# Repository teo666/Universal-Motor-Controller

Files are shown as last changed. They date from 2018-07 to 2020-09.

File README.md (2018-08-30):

# What Universal-Motor-Controller is

Universal-Motor-Controller (UMC) is an Arduino based software and hardware intended to drive universal brushed motor, like many circuit based on TDA1085.

# Main components

UMC consist of two parts:
- software: a C/C++ code running on Atmel Atmega-328p (Arduino Uno and compatibles boards)
- hardware: divided in three parts
    - zero crossing detector circuit (zcd), used for synchronize Arduino on main power
    - power circuit, used for feed motor
    - feedback circuit, used for monitoring the speed of the motor and adjust feed power consequently

# Working principle

Image below shows UMC's working diagram

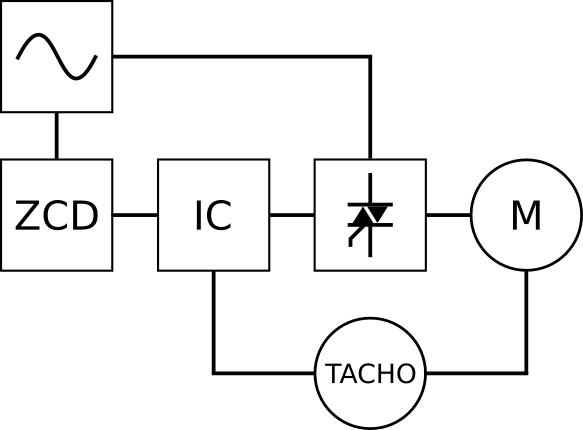
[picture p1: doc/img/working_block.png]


- The main power is connected to zero crossing detector circuit that transform sine wave signal to a square wave signal and send it to IC, main power source is conneted to motor power switching circuit
- IC is an Atmega-328p
- the power switching circuit is for made up of a triac, it controls the power of the motor and it is drived by IC
- the tacho is the feedback circuit of the system, it generate a signal to IC in relation to motor speed.

The main target of the driver is to changes power feeding the motor to prevent slowdowns when the load changes, to achieve this goal IC analyzes signal coming from tachogenerator and consequntly it swiches triac.

For a correct switching, IC has to know the exact phase of main power source, this is guarantee by ZCD circuit.

ZCD generates a square wave with a doubled frequency compared to main power source frequency, in my case, considering a 50Hz main frequency it generate a square wave of 100Hz.
This signal is connected to a special pin of the Atmega that is able to recognize the rising edge of ZCD output signal and rise a hardware interrupt that freeze the current program execution flow and execute a special routine. This mechanism allow to the Atmega to know when the main power source has reached the value of 0 volt so that it can syncronyze the motor power circuit.

(For a more comprensive and detailed guide about triac working principle read https://en.wikipedia.org/wiki/Thyristor and https://en.wikipedia.org/wiki/TRIAC)

The above simple mechanism is enough to drive motors and it allows to change their speed with a potentiometer, for example we could read an analog value and map it along the time interval punctuated by two rising edge coming from ZCD circuit, and switch triac in relation to that value. The figure below illustrate that mechanism

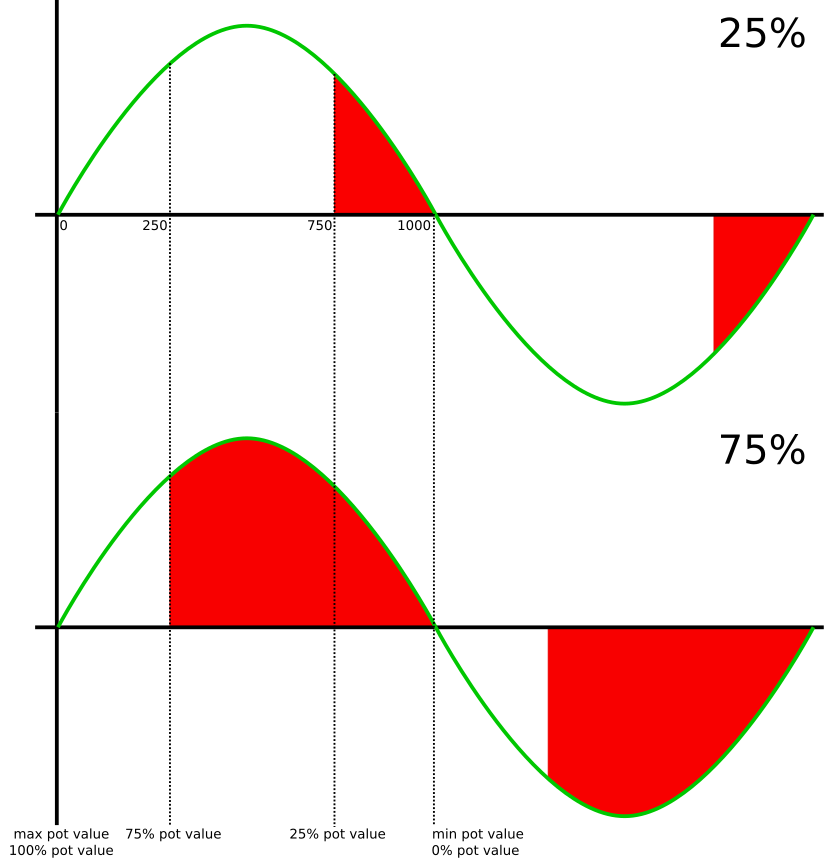
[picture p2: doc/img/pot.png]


Suppose to have a potentiometer to adjust the motor power: if potentiometer is turned to left the motor power decrease otherwise it increase. To achive that we have to change the switching point of triac inside main power source half period. In our case the potentiometer is connected to one of the avr analog input pin and readed value from potentiometer is mapped into a value between 0 and 999, and assume that we divide the semiperiord in 999 slice with the same width going from 0 to 999.

Now, if the potentiometer read value is 0 we want the mimimun motor power so we have to leave triac turned off.
If potentiometer get a value of 999 the desire power is maximum, we have to excite trigger immidiatly after the 0 volt point, or equivalentemente at 0th slice.
For any other value of potentiometer we have to trigger triac at slice numbered as (999 - pot_value) where pot_value is the value readed from potentiometer.

At this point the main question is: how divide half period into equal slices to know when turn on triac?
The response is: with timers.

Basically timers are hardware device enclosed into many ICs (avrs too) that can be used to count time. Think about timer like an unsigned variable going from 0 to a max value, and its content is increased by one (or decreased by one, or set to zero) every time that something happen, the something that happens is the clock signal, eventually scaled by a constant. Hardware can be configured to execute some special code (exactly like interrupt mechanism previously described) each time timer value reaches a special value, for example its maximum value.

The Atmega-328p (like arduino) is usually clocked with a 16MHz crystal oscillator, suppose to scale the clock with a 128 factor and use that signal to feed a 8bit timer. With that configuration timer increase its value by one every 
1 / (16e6 / 128) = 0.000008 seconds or 8 microseconds, and suppose to configure hardware to execute the special code (called Interrupt Service Routine or ISR) every time timer reach maximum value that in a 8bit configuration is 255, and the ISR increase the `tick_count` variable value by one starting from 0.

After 256 * 8 = 2048 microseconds `tick_count` value is incresed to 1  
After 4096 microsecond `tick_count` value is 2  
After 6144 microsecond `tick_count` value is 3  
After 8192 microsecond `tick_count` value is 4  
...  
After 999424 microseconds `tick_count` value is 488

or equivalently, when `tick_count` is 488 approximately a seconds is passed, that is how Arduino libraries implements millis, micros and delay functions.

The idea that we use is the same: increase a variable by one periodically inside the timer's overflow ISR (executed when timer reaches its maximum value) and reset it when ZCD find a zero volt point... then reapeat.

Go back to potentiometer example. Suppose to be immediatly after a 0 volt point and ZCD has reset our variable, and also use following condition to turn on triac.

``` c++
if( tick_count >= (999 - pot_value)){
    turn_on_triac();
}
```
- if potentiometer is set to maximum value (999) then (999 - pot_value) = 0, our variable is greater or equal to 0 and the triac is turned on
- if potentiometer is set to minimum value (0) then (999 - pot_value) = 999, our variable is less than 999 and the triac remains off
- likewise intermediate values

when next 0 volt poin occur, ZCD interrupt is executed, the `tick_count` variable is reset, and the process is repeated.

At this point we have a mixture of software and hardware that is commoly called *dimmer*, a device that can change power given to a load turning a potentiometer, those kind of devices are usually used to change halogen lamps brightness, the next step is feedback circuit integration.

The feedback circuit allow system to react to load changes and increase motor power to avoid slowdowns. The feedback circuit receives a signal coming from the tachogenerator of the motor, make some process on it and send it to IC.
The tachogenerator signal is commonly an AC sine wave signal that increase its frequency and voltage as the speed increases, so it is possible use frequency or voltage or event both together to analyze the speed of the motor, in UMC frequency is used.
The tacho AC signal is converted to an AC square wave signal and then only the positive component is taken, giving to IC a DC square wave signal. The figure below show the tacho processing signal

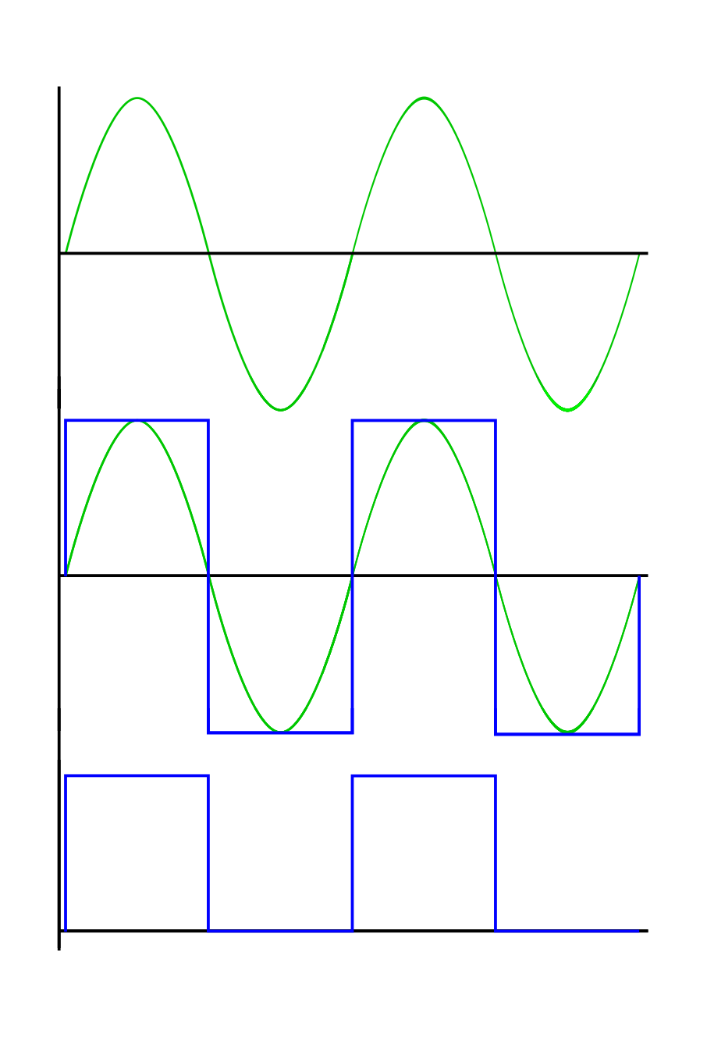
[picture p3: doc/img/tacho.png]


Once IC receives the feedback signal it has to get its frequency to know the actual speed motor and change its power consequently. To do that UMC use the same tecnique used for ZCD: interrupt mechanism.

Each time feedback signal goes from low to high (rising edge) IC's hardware generates an interrupt, the normal code execution is paused and associated ISR is executed.  
Previously we have talked about measuring signal frequency, in truth we do not need know the exact frequency, instead just a value related to frequency on wich make a comparison.  
At this point is relatively simple to get an evaluation of feedback signal frequency. Do you remember the use of timer for periodically check if triac has to be turned on? Ok, we use the same routine for increase a counter associated to feedback signal and we will reset that value in ISR associated to feedback rising edge event. In that manner we have a value related to frequency: the higher the frequency (motor speed) the lower is the couter.

At this point IC has all needed parameter for controlling power motor, and for do that we use a PID controller, you can read more about PID controller on [Wikipedia](https://en.wikipedia.org/wiki/PID_controller), about 
[used library](https://playground.arduino.cc/Code/PIDLibrary) and 
[detailed library explanation](http://brettbeauregard.com/blog/2011/04/improving-the-beginners-pid-introduction/).

# Hardware
DISCLAIMER: I am not a electrical engineer and all these circuits were taken on web and put together with a limited knowledge of them. If you have suggest to improve them and UMC you are welcome.

Below are reported the schematic circuits used in UMC
### Zero crossing detector circuit



note: VCC is 5 volt, all resistor are 1/4 watt,T1 and OK1 can be changed with equivalent components.  
PORTD,PIN2 is equivalent to pin 2 on Arduino-UNO board

### Motor power circuit



note: all resisor are 1/4 watt except R8 that is 1 watt (instead one 100 ohm resistor i recilced four 470 ohm resistor in parallel) , C3 must have appropriate galvanic isolation, for T2 I used a BTB16 couse BT138 gave me some problem.  

PORTD,PIN7 is equivalent to pin 7 on Arduino-UNO board

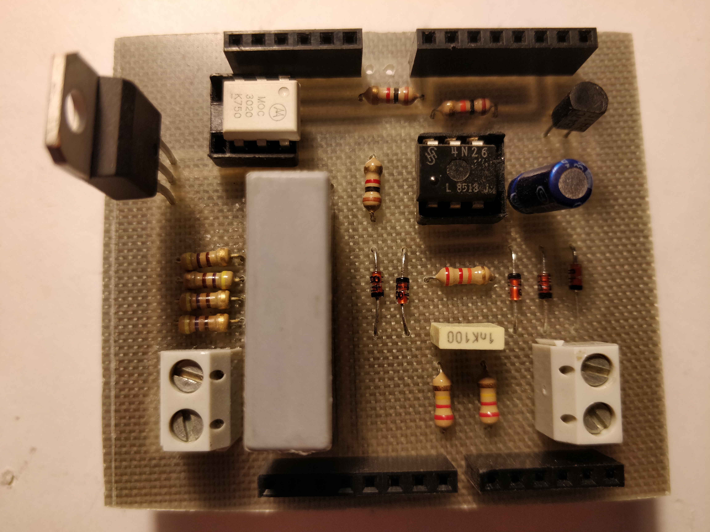
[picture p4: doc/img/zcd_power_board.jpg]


note: zcd and motor power circuits on same pcb



### Feedback circuit

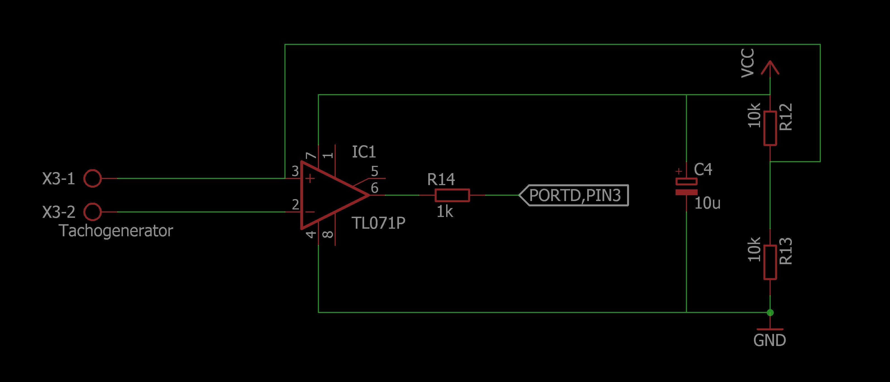
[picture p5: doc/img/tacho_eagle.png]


note: note: all resisor are 1/4 watt, Vcc is 9 volts, IC1 can be replaced with another opamp  

PORTD,PIN3 is equivalent to pin 3 on Arduino-UNO board

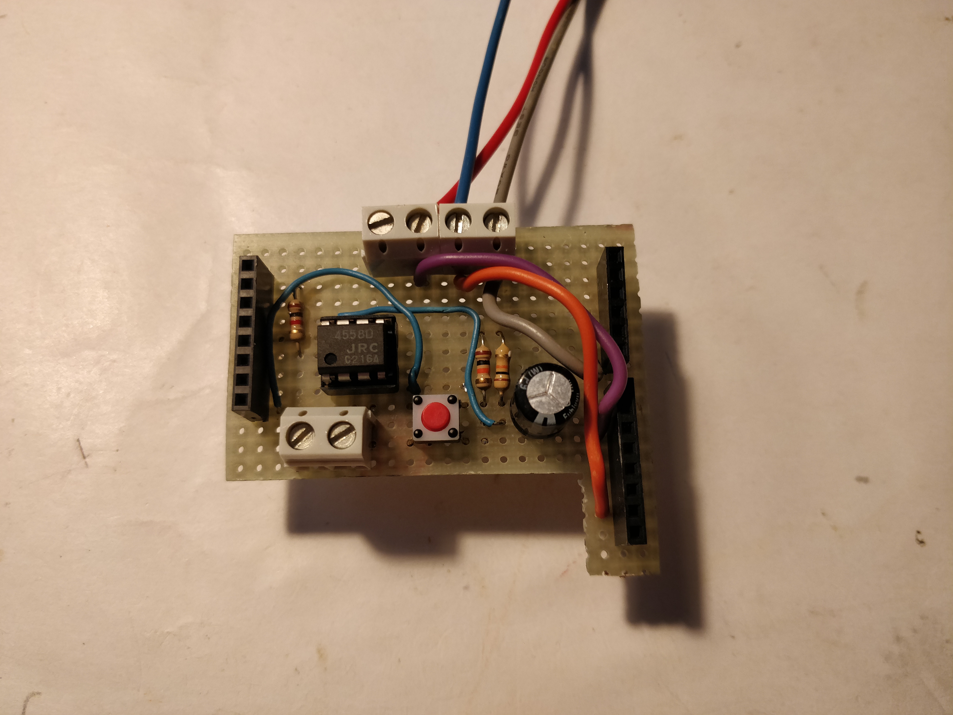
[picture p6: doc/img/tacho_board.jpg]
  

this board contains the potentiometer connector too and a push button connected to PORTD,PIN6 that is equivalent to pin 6 on Arduino-UNO board. We will talk about the push button later.

All together

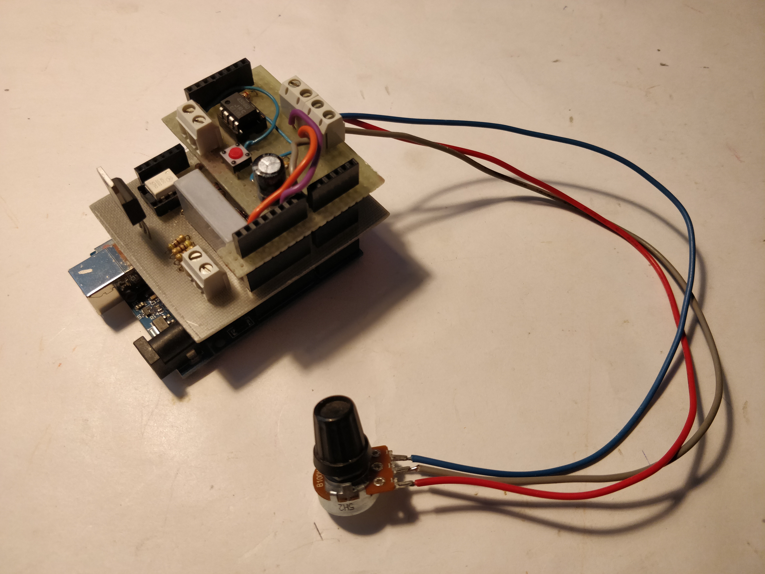
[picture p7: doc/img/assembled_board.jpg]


### Motor connection

Usually universal motor has six cable:
- two for the rotor
- two for the stator
- two for the tachogenerator

The cables of tachogenerator have to be connected to the tacho circuit and the order is irrilevant.  
The rotor and stator windings have to be connected in series togheter with main AC power source and power circuit, as show below.  
**NOTE: swap stator terminals to change rotation direction of the motor.**

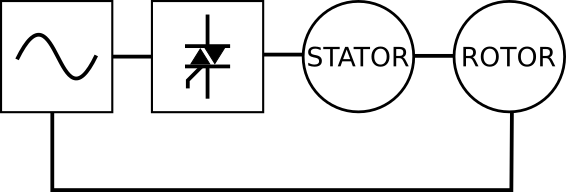
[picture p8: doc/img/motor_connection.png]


### UMC box

This photo show UMC with its box, taken from an old ATX power supply

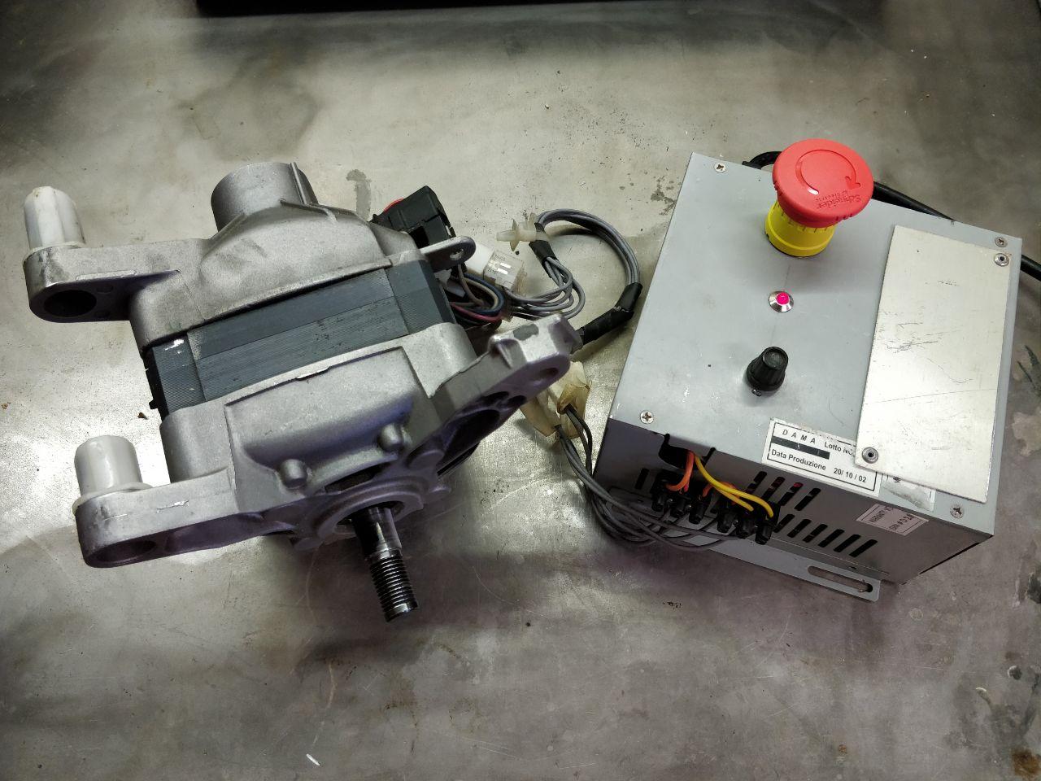
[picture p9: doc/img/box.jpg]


### Demo video

This [video](https://youtu.be/NKULTa6kquY) is a demonstration about UMC capabilities.  
This [video](https://youtu.be/l1mFbbu4X3Q) show capabilities of UMC on low speed.  
These two [video1](https://youtu.be/YVdLVX_Wkz4) and [video2](https://youtu.be/LLw0HUfIIPY) show a motor driven by UMC connected to a bench grindstone disconnected from main power.  
This [video](https://youtu.be/WyjBL2rSP_o) show UMC with current measurement.
# Speed limiter

UMC comes with a spftearec based speed limiter. Speed limiter use the feedback signal to to achive this goal. Speed limiter is usefull because it allow to map all potentiometer turning range inside the desired motor speed limits.  
In some application we could need maximum motor speed around 2000 rmp and in other 4000 rmp, but we want reach those speed when potentiometer is completely at the most, and leave hardware and software as they are, without needs of modifications.
At the moment it is possible limit the speed only during avr's boot process using the *programming button*.
Programming Button is a push button that if pressed connect PORTD,PIN6 (pin 6 of Arduino Uno) to ground, and allow us to set limit speed values (low and high), these values are stored in avr's EEPROM so they are accessible at the next restart, whitout needs to set up them every time.

**CAUTION: programming button is used to switch from automatic to manual mode too. Manual mode allow to disable the feedback circuit and use UMC as a simple dimmer. Suppose to have upper speed limit set to 1000 rpm and runnign motor with this speed, so with potentiometer at maximum. If you press programming button in this condition the motor will receice all possible power and its speed will increase with possible motor or equipment damage.**

### Usage

- Connect Arduino to PC, on Arduino IDE open serial monitor (ensure all parameter are correct: serial port, board etc)
- press and hold the *programming button*
- reset the board keeping *programming button* pressed
- read serial monitor keeping *programming button* pressed and follow printed instructions

At the end of process if you turn potentiometer the speed motor is limeted inside selected range.

# Configuration

Attention: before reading this section be sure that you know what PID parameters are, otherwise follow links at the end of "Working principle" section.

With 1.0.1 version UMC comes with dynamic PID parameter change. Basically UMC can change its PID parameter in relation to motor speed, in fact some parameters that work correctly at a fixed speed can be wrong at lower or higher speed, making UMC non-reactive or causing rotation spikes.  
To achive this gol the constructor of PID library take extra parameters, such as a function, that it is called inside `compute()` PID function to get the correct PID parameters.
That function is named `search` and it is placed inside `configuration.h` file. You have to customize `search` function to satisfy your preferences.
The signature of `search` function is the following
``` c++
CoefficientPtr search() {
    ...
}
```
it must return a `CoefficientPtr` that is define in `PID_ASYNC.h` as
``` c++
typedef struct _coefficient {
  double Kp;
  double Ki;
  double Kd;
} Coefficient;

typedef Coefficient *CoefficientPtr;
```
Inside `configuration.h` file you can find an example of search function that meets my needs, the code is the following
``` c++
//static parameter declaration
Coefficient k_param[9];

/**
* function called inside setup() to fetch parameter
*/
void init_params() {
  k_param[0].Kp = 0.3;
  k_param[0].Ki = 0.0001;
  k_param[0].Kd = 0;

  k_param[1].Kp = 0.8;
  k_param[1].Ki = 0.0001;
  k_param[1].Kd = 0;

  k_param[2].Kp = 1;
  k_param[2].Ki = 0.0001;
  k_param[2].Kd = 0;

  k_param[3].Kp = 1.5;
  k_param[3].Ki = 0.0002;
  k_param[3].Kd = 0;

  k_param[4].Kp = 2;
  k_param[4].Ki = 0.0002;
  k_param[4].Kd = 0;

  k_param[5].Kp = 3;
  k_param[5].Ki = 0.0002;
  k_param[5].Kd = 0;

  k_param[6].Kp = 3;
  k_param[6].Ki = 0.001;
  k_param[6].Kd = 0;

  k_param[7].Kp = 3;
  k_param[7].Ki = 0.001;
  k_param[7].Kd = 0;

  k_param[8].Kp = 7;
  k_param[8].Ki = 0.002;
  k_param[8].Kd = 0;
}

/**
 * function called inside compute() PID function
 * get the minimum value from Setpoint and Input 
 * and use it to chose the correct parameters
 */
CoefficientPtr search() {
  double _val = min(Setpoint, Input);
  uint8_t index = 0;

  if (_val >= 550) {
    index = 0;
  } else if (_val >= 500 && _val < 550) {
    index = 1;
  } else if (_val >= 450 && _val < 500) {
    index = 2;
  } else if (_val >= 400 && _val < 450) {
    index = 3;
  } else if (_val >= 350 && _val < 400) {
    index = 4;
  } else if (_val >= 250 && _val < 350) {
    index = 5;
  } else if (_val >= 200 && _val < 250) {
    index = 6;
  } else if (_val >= 150 && _val < 200) {
    index = 7;
  } else if (_val <= 150) {
    index = 8;
  }
  return &k_param[index];
}
```

- on the top an array is declared to hold different `Coefficient` structures,
- the method `init_params()` is declared, it allow you to initialize the array, in the above code it is initialized statically, but you could need to read some value from EEPROM and store them inside it.
- the `search` function is declared, it is responsible for providing dynamic parameters to PID in relation to the speed of the motor.

Inside `configuration.h` file you have access to all available global variables, for example Setpoint, Input and Output PID variables, but **DON'T MODIFY THEM, JUST READ THEM**.

Ok... but, where those value (500, 350 and so on) come from?  
They come from **test mode**. *test mode* allow you to run UMC, change speed with potentiometer and set dynamically PID parameters to test them with no need to flash the ROM of the avr everytime.
To use *test mode* uncomment first line in the `Universal_Motor_Controller.ino` file to get
``` c++
#define TEST_MODE
```
and then flash avr.  
Open serial monitor, current *Setpoint*, *Input* and *Output* values are shown. You can change the *kp*, *ki* and *kd* parameters in serial input, giving the command
``` bash
<param_name> <value>
```
where `param_name` can be 
``` bash
kp
ki
kd
```
to set respectively proportional, integral or derivative parameter  
and `value` is a floating point value like 
``` bash
0.0002
```
**ATTENTION: THERE IS ONLY ONE SPACE BERTWEEN TWO ARGUMENTS** 

**ATTENTION: PARAMETERS MUST BE GIVEN SEPARATELY, YOU CAN'T SET THEM ALL TOGHETER, ONLY ONE BY ONE**  

**ATTENTION: K-VALUES ARE SHOWN WITH EIGHT DECIMAL DIGIT PRECISION**

While program runs it shows current *Setpoint* and *Input* values that can be used to discriminate the correct PID weights inside *search* function, that is where previous unknow numbers come from. With these value it is possible to see how UMC react to load change, considering that *Input* value should be near as possible to *Setpoint*.

Once done you can create your own `init_params` and `search` function and comment first line into `Universal_Motor_Controller.ino` file to get
``` c++
//#define TEST_MODE
```
and flash again.

Enjoy!

# Changelog

v1.0.1
- UMC comes with its own version of PID library, it is heavily based on Brett Beauregard's PID library  
(library link:  https://playground.arduino.cc/Code/PIDLibrary  
email: <br3ttb@gmail.com>  
library explanation: http://brettbeauregard.com/blog/2011/04/improving-the-beginners-pid-introduction/): the new version is basically identical to Brett Beauregard's version except for the facts that it is now asynchronous and some unused methods are deleted.
- UMC can now change its PID parameters dynamically, related to motor speed.
- Improved motor stability on low speed
- Code revisiting.
- UMC comes now with a test mode usefull for calibration.

v1.0.2
- Improved initial frequency calculation by decreasing needed time
- Added zero crossing detection circuit fail detection condition. Before this version when a zcd circuit fail occur UMC gave all power to the motor
- Added motor hang/stop detection condition (early version to use with caution)
- UMC is now (partially) invulnerable to the power line frequency changes
- Added eagle project files including circuit schematic and board layout

# Known problems and Improvements

This is an early UMC version and there are many things to improve.  
I hope that someone will find this project interesting helping me (and diyers community) to improve its capabilities.

### Higher priority 
- Slow start integration (via PID controller)
- Allow rotation inversion (require hardware modification and hang/stop detection)

### Lower priority

- Lower speed limit can't be set to 0rpm.
- Program lives as it is, there isn't an Object Oriented Programming model and integrations with other libraries are difficult due to time dependent application nature.
- UMC doesn't allow connect multiple motor due low number of Atmega-328p interrupt pins. One is necessary for ZCD circuit the other for feedback circuit. I'm trying to remove this lack using a frequncy to analog converter that technically will allow drive up to six motor. Should be possible monitor feedback signal without the need of interrupt pin by checking it periodically inside timer's ISR, but I have not tested this method yet.
- OOP usage is releted to the above two problems.

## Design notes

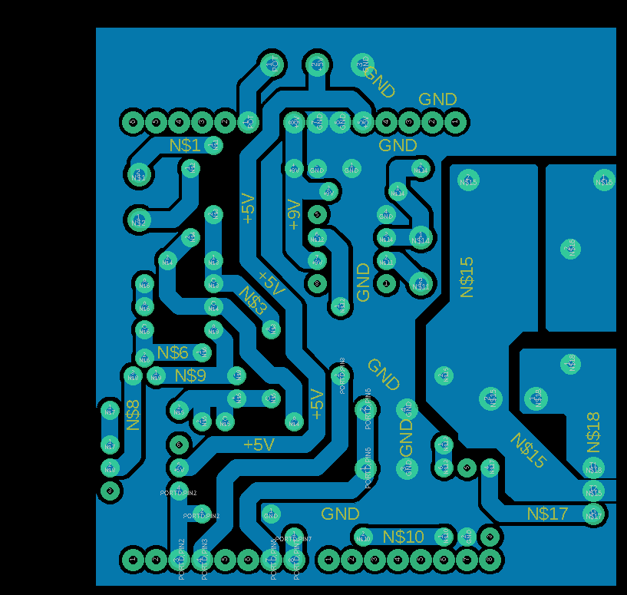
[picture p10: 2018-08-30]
doc/img/circuit-net.png

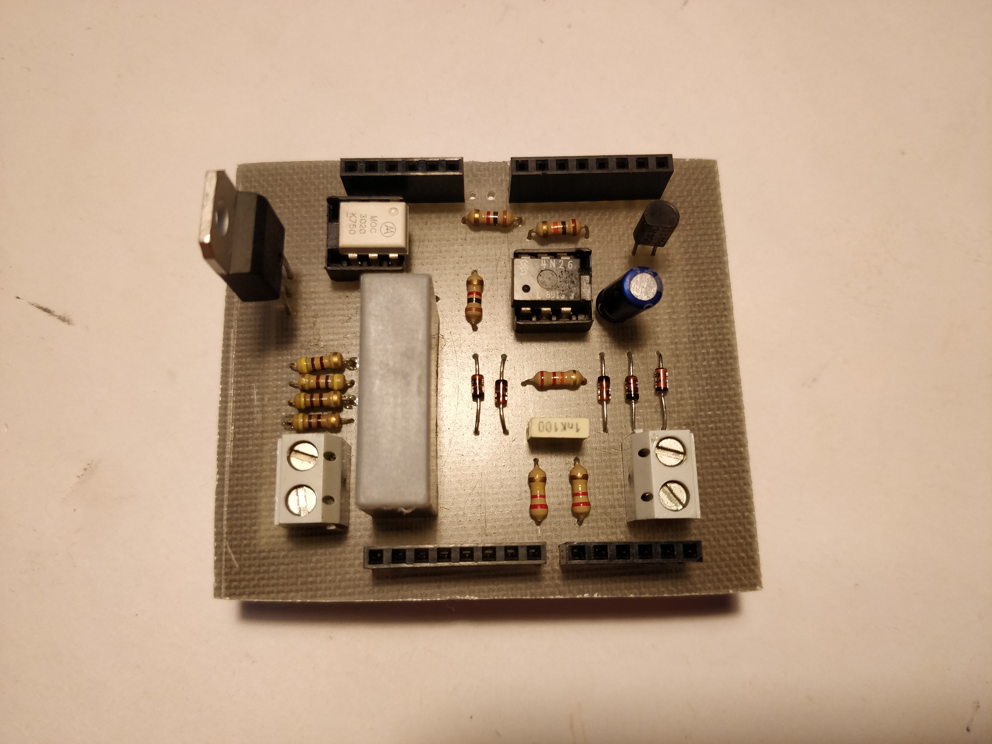
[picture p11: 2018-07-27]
doc/img/zcd_small_board.jpg

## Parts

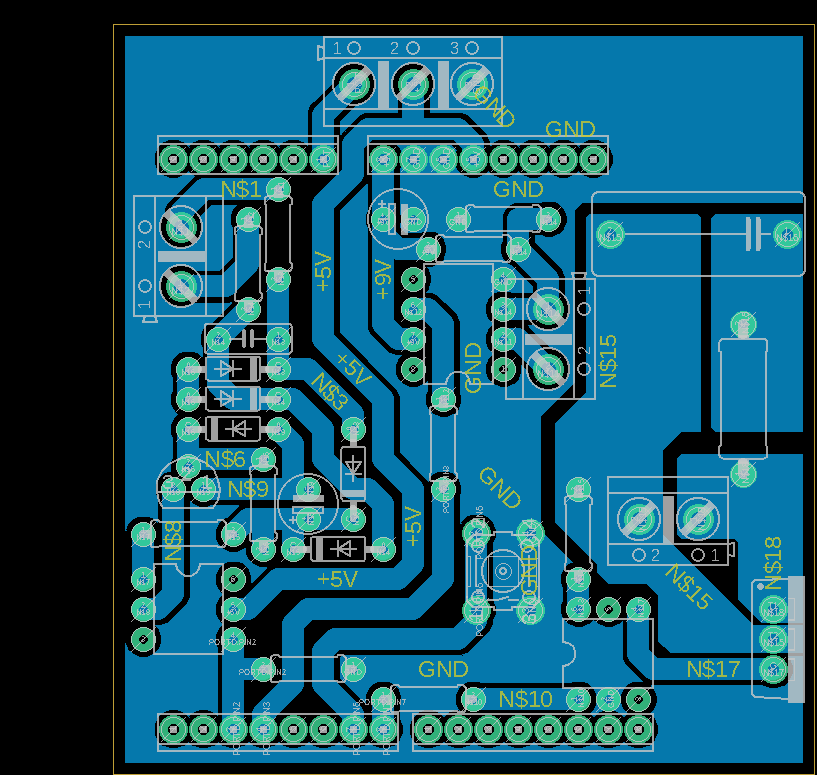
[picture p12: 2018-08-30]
doc/img/circuit-net-component.png

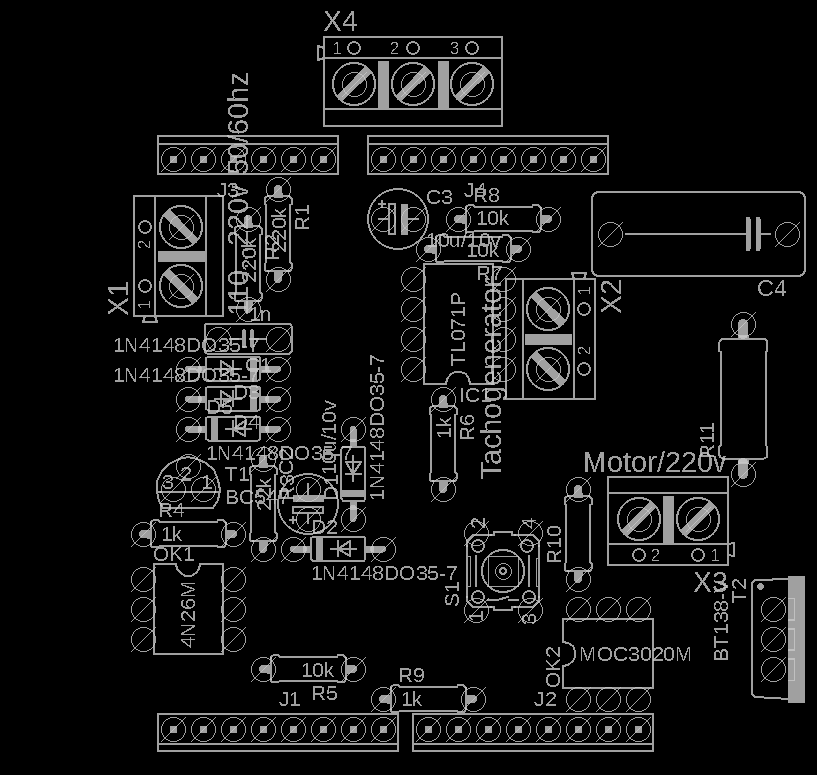
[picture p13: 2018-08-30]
doc/img/circuit-component.png

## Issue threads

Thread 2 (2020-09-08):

Compiling trouble

Baravantan, 2020-09-08:
First of all thank you for sharing your work.
I tried to compile with the "TEST_MODE" option but I get an error and it doesn't compile.
Also, if I leave the option commented out, I can compile in, but when I feed the circuit, the motor slowly begins to accelerate whatever the position of the potentiometer.
I checked the input signals (ZCD, TACHO, POT) and they seems normal.

versione 1.0.2 | Arduino:1.8.12 (Linux), Scheda:"Arduino Nano, ATmega328P (Old Bootloader)"

teo666, 2020-09-09:
Hi @Baravantan !
Thanks to you for use and improve this code. I hope it can be usefull for you.

1) I confirm the compile error, the problem was caused due to a wrong place regards macroes definition. I have updated the repo.
2) Have you set the speed limit values during start up? These value should be printed in console during board sturtup. Check them, if they are correct, try to enable test mode, change PID parameters and check if the motor react to these changes.

Let me know

Baravantan, 2020-09-09:
Hi @teo666 and thanks for your reply.
I was unable to set the speed limits values because, on power ON, the motor begins to accelerate whatever the position of the potentiometer, until it reaches a dangerous rpm. then I cannot set the minimum and maximum desired values. Unfortunately, my knowledge of the software is somewhat limited.
I built a circuit following the diagram you published, and connected it to a motor recovered from a Bosch washing machine, not better identified. I measured the signals on the tachometer more carefully and I detected **168Vpp** (!!)
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
and, on PORTD pin3, a signal at 25+ kHz and **8 Vpp** which I think is too much for Arduino.
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
Then, I lowered the supply voltage of the OP amp from 9V to 5.5V, obtaining the same signal at the output but with the correct level.
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
May be that my motor produces a too high TACHO signal, and saturate (or destroy!) the OP amp input?
I will do other tests. If you have any suggestion, please help me. Thanks

teo666, 2020-09-12:
Hi @Baravantan
I admin that my circuit is not perfect due I am a software engineer but  not electrical, it could be improved and if you have suggestion you are welcome.

The tacho circuit is intended to work in saturation, I use this method to convert the tacho signal into digital signal that is more
easy to analize in arduino thanks to interrups.

However you are describing an unexpected behavior in UMC. In fact when programming phase start the output pin should be disabled preventing motor to start spin.
In this phase the main line frequency is calculated and the output motor is directly drived by potentiometer value. So keeping potentiometer
at lowest value (or ground its input) should disable the output motor pin, and increasing the potentiometer value shoud give the ability to modulate motor speed whit no PID control.

So I think there should be upstream problem, and preceed by step, ensuring all circuits (and software) are working properly. First of all i suggest to make programming mode working proprerty. It is usefull cause its behavior is like a simple triac circuit and can be used to drive bulb lamp (no led or flourescent lamp) avoiding keep attention on motor speed.

I remember that to get in programming mode programming button must be pressed before arduino start booting, and keep it pressend until "Programming mode" appear in serial monitor.

At this point the main line frequency is calculated the result is printed on monitor (its  value is not printed ad frequency but as timer clock tick) and UMC ask to set limit speed values, with oscilloscope should be possible see on ZCD circuit output a signal as in following image. At this point tacho signal is useless (except if we continue with setting limit speed) and circuit could be used as a simple triac circuit.
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

Are you able to confirm these step?

PS: ZCD signal can be always measured to check it works properly, even in disconnected

The next step is check if arduino can trigger interrupt propertly
Obviously i take for granted that circuit is correct

Baravantan, 2020-09-13:
Hi, @teo666
Ok, I followed the suggested procedure:
By keeping S1 pressed at boot, it enters the programming mode correctly:
`Calculating frequency ...`
`Number of ticks per half period: 617`
`Programming mode`
`Release programming button, please`
BUT the engine always runs.
IF instead I press S1 when the sketch is running, with the POT at zero, the output goes to zero.

I tried, as suggested, to connect a light bulb instead of the motor (great suggestion!).
I took a couple of screenshots: ch1 ZCD (1 yellow) Pin2 || ch2 Pin OC (2 light blue) || ch3 ACL (3 fuchsia) || S1 OFF || POT 50%
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

the signal on OC (2) turns off after 640uS from the crossing of the zero of AC L (3), when the next half-wave has reached 50V, thus triggering the triac also for the next half-cycle and therefore leaving the output always on.
By holding S1 and turning the POT, the length of the signal on the OC changes to the left, but it always goes out in the same point, except when I turn the POT to zero: in this case the signal on the OC disappears completely, and then the output turns off .
What I would do, if I were able, is to anticipate the shutdown of OC (2) before the zero crossing.
What I don't understand is why the sketch on your circuit works, but on mine it doesn't.
I also double-checked the connections and tried to upload the sketch to Arduino UNO as well (I'm currently using Nano), with identical behavior.
I hope this information is somehow useful.
Thanks for your help.

Baravantan, 2020-09-14:
Hi, @teo666
Important update
I built a really rough circuit, with the aim of getting a signal when AC is below a certain voltage level, and then around the zero crossing.
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
The pulse I get is not that great (1 yellow), but now the circuit works in dimmer mode!
The ZCD pulse now arrives before the zero crossing, and consequently also the OC pin signal (2 light blue) turns off before it, but obviously not the triac, which continues to conduct up to the ZC.
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
Obviously, the circuit now needs some fine tuning and some calculations; what do you think about it?

Baravantan, 2020-09-15:
My idea (leaving the circuit as is) is to transform the output to the triac from variable to fixed width (some tens of µS) leaving unchanged the moment when it turns on. I tried to change it in the code, eg.
`if (tick_after_zcd > xx) {TURN_OFF_TRIAC (); triac_state = 0;}`
but I did not succeed.

teo666, 2020-09-15:
Hi @Baravantan
These images are extremely usefull because they describe the working princile, and help to find the error.

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

Good!

Lets analize [this](https://user-images.githubusercontent.com/11626439/93020077-e1a09400-f5e3-11ea-9e5a-24b2b3289924.png) image, and exlude momentary the fuchsia channel.
The yellow signal represent ZCD output and light blue triac triggering signal.

The fact that light blue signal overlaps the yellow one is a desired behavior, and this confirm that the interrupt code
is working correctly. This overlap is caused by the fact that the software make sure that zero crossing point is reached correctly and it is effectively the correct one.
This mechanism is used to avoid that arduino recognize signal spikes in ZCD signal as wrong zero point.

The following block code is responsible of this behavior, increasing the value (10) in the condition will delay triac output switch off.
If 0 is used no correction will be used and falling edge of triac output will coincide with rising edge of ZDC signal, and using too much higher value will
fall triac output switch off after the zero crossing point, thus making triac always on.

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

The ZCD circuit that you have used confirm this situation, except the fact that it doesn't give a sqaure wave signal, we can see the same overlapping situation
in [this](https://user-images.githubusercontent.com/11626439/93047871-2705a580-f666-11ea-9664-b1d292cad140.png image.

At this point cosider the [image](https://user-images.githubusercontent.com/11626439/93020077-e1a09400-f5e3-11ea-9e5a-24b2b3289924.png) with fuchsia channel.

My ZCD circuit is based on [this](https://dextrel.net/design-ideas-2/mains-zero-crossing-detector.html) and as the author explain it should
trigger around zero volt point. BUT previous image seems not to confirm this situation, in fact the yellow risign edge is shifted to the right.

So I can assert that ZCD is not working propertly. Your circuit insead is working correctly becuase the yellow spike is centered on zero point.

At this point we have many way to proceed, some are solutions, others dummies solutions:

Solution:
    Change ZCD circuit.

Dummy solutions:
    Turn off triac output signal earlier for example after triac has entered into conduction state (I don't consider this as solution becuase does not resolve the sync problem of ZCD signal)

teo666, 2020-09-15:
> My idea (leaving the circuit as is) is to transform the output to the triac from variable to fixed width (some tens of µS) leaving unchanged the moment when it turns on. I tried to change it in the code, eg.
> `if (tick_after_zcd > xx) {TURN_OFF_TRIAC (); triac_state = 0;}`
> but I did not succeed.

I can suggest this fast, brutal and not tested code

`if (triac_state) {`
`TURN_OFF_TRIAC();`
` }`

and put it immediatly BEFORE this code (before triac hes been swiched on)

`if (tick_after_zcd >= output && !triac_state) {`
`    // accendi il triac`
`    TURN_ON_TRIAC();`
`    triac_state = 1;`
`  }`

Let me know
Teo

Baravantan, 2020-09-16:
It finally works as expected! and leaving yours circuit and sw intact.
Solution:
Put the correct values of the components on the circuit.

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

As I feared, this was human error: for reasons too long to explain, I put C2 100x the required value. I'm sorry.
"C2 forms together with R1 and R2 a first-order low pass filter (...) By decreasing the 1/f frequency of this filter (...) the ZC-pulse will be delayed in relation to the real mains zero crossings"

Thank you very much for the time you have dedicated to me to find the error, as well as your indications were very useful to understand how your circuit works.

Giovanni

Closed 2020-09-16.

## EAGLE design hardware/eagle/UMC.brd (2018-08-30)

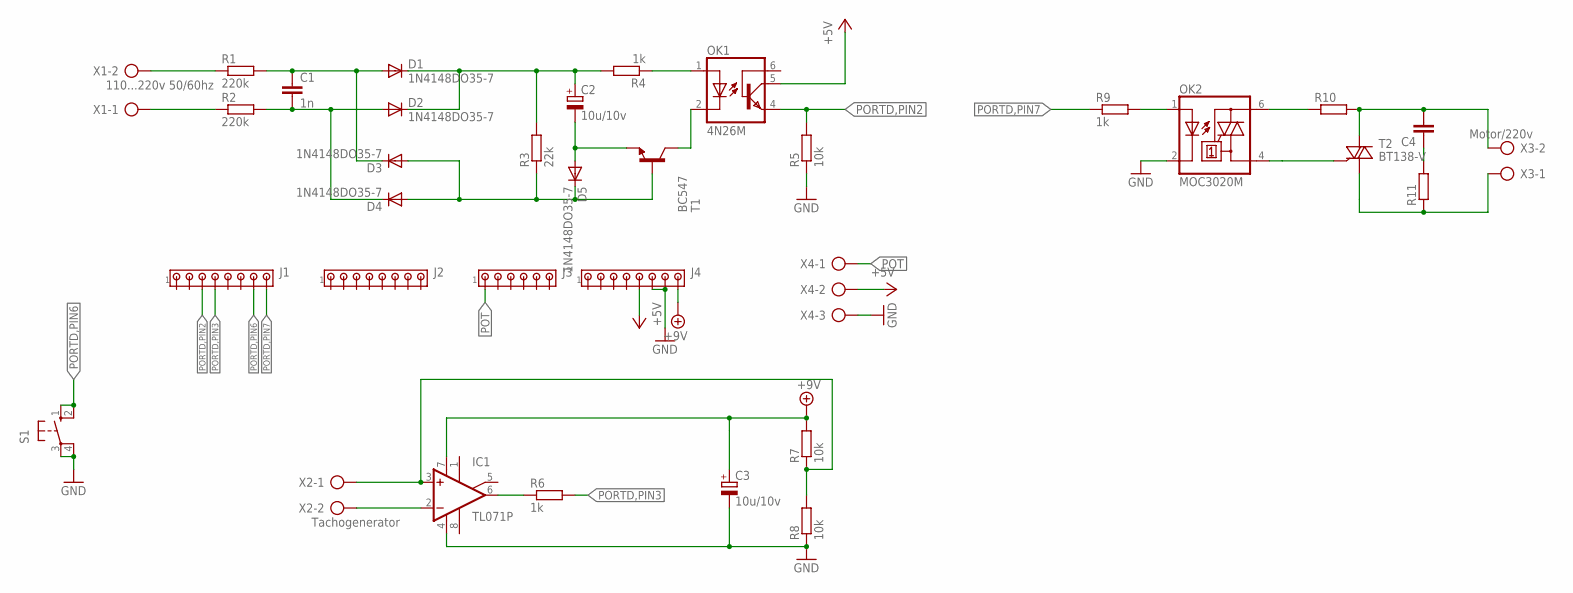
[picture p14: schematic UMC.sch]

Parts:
C1: 1n; C5B2.5
C2, C3: 10u/10v; E2,5-5
C4: C15/7; C15B7
D1, D2, D3, D4, D5: 1N4148DO35-7; DO35-7
IC1: TL071P; DIL08
J1, J2, J4: MTA08-100; 10X08MTA
J3: MTA06-100; 10X06MTA
OK1: 4N26M; DIL06
OK2: MOC3020M; DIL06
R1, R2: 220k; 0207/7
R3: 22k; 0207/7
R4, R6, R9: 1k; 0207/7
R5, R7, R8: 10k; 0207/7
R10: R-EU_0207/7; 0207/7
R11: R-EU_0411/12; 0411/12
S1: 10-XX; B3F-10XX
T1: BC547; TO92
T2: BT138-V; TO220BV
X1: 110...220v 50/60hz; AK500/2
X2: Tachogenerator; AK500/2
X3: Motor/220v; AK500/2
X4: AK500/3

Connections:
+5V: J4.5, OK1.5 (COL), X4.2
+9V: C3.+, IC1.7 (V+), J4.8, R7.2
GND: C3.-, IC1.4 (V-), J4.6, J4.7, OK2.2 (C), R5.1, R8.1, S1.3, S1.4 (P1), X4.3
unnamed: R1.1, X1.2
unnamed: R2.1, X1.1
unnamed: C1.1, D1.A, D3.C, R1.2
unnamed: C1.2, D2.A, D4.C, R2.2
unnamed: C2.+, D1.C, D2.C, R3.2, R4.2
unnamed: D3.A, D4.A, D5.C, R3.1, T1.2 (B)
unnamed: OK1.1 (A), R4.1
unnamed: OK1.2 (C), T1.3 (C)
unnamed: C2.-, D5.A, T1.1 (E)
unnamed: OK2.1 (A), R9.2
unnamed: IC1.2 (-IN), X2.2
unnamed: IC1.6 (OUT), R6.1
unnamed: OK2.6 (A2), R10.1
unnamed: IC1.3 (+IN), R7.1, R8.2, X2.1
unnamed: C4.2, R10.2, T2.T2 (A2), X3.2
unnamed: C4.1, R11.2
unnamed: OK2.4 (A1), T2.G
unnamed: R11.1, T2.T1 (A1), X3.1
PORTD,PIN2: J1.3, OK1.4 (EMI), R5.2
PORTD,PIN3: J1.4, R6.2
PORTD,PIN6: J1.7, S1.1 (S), S1.2 (S1)
PORTD,PIN7: J1.8, R9.1
POT: J3.1, X4.1

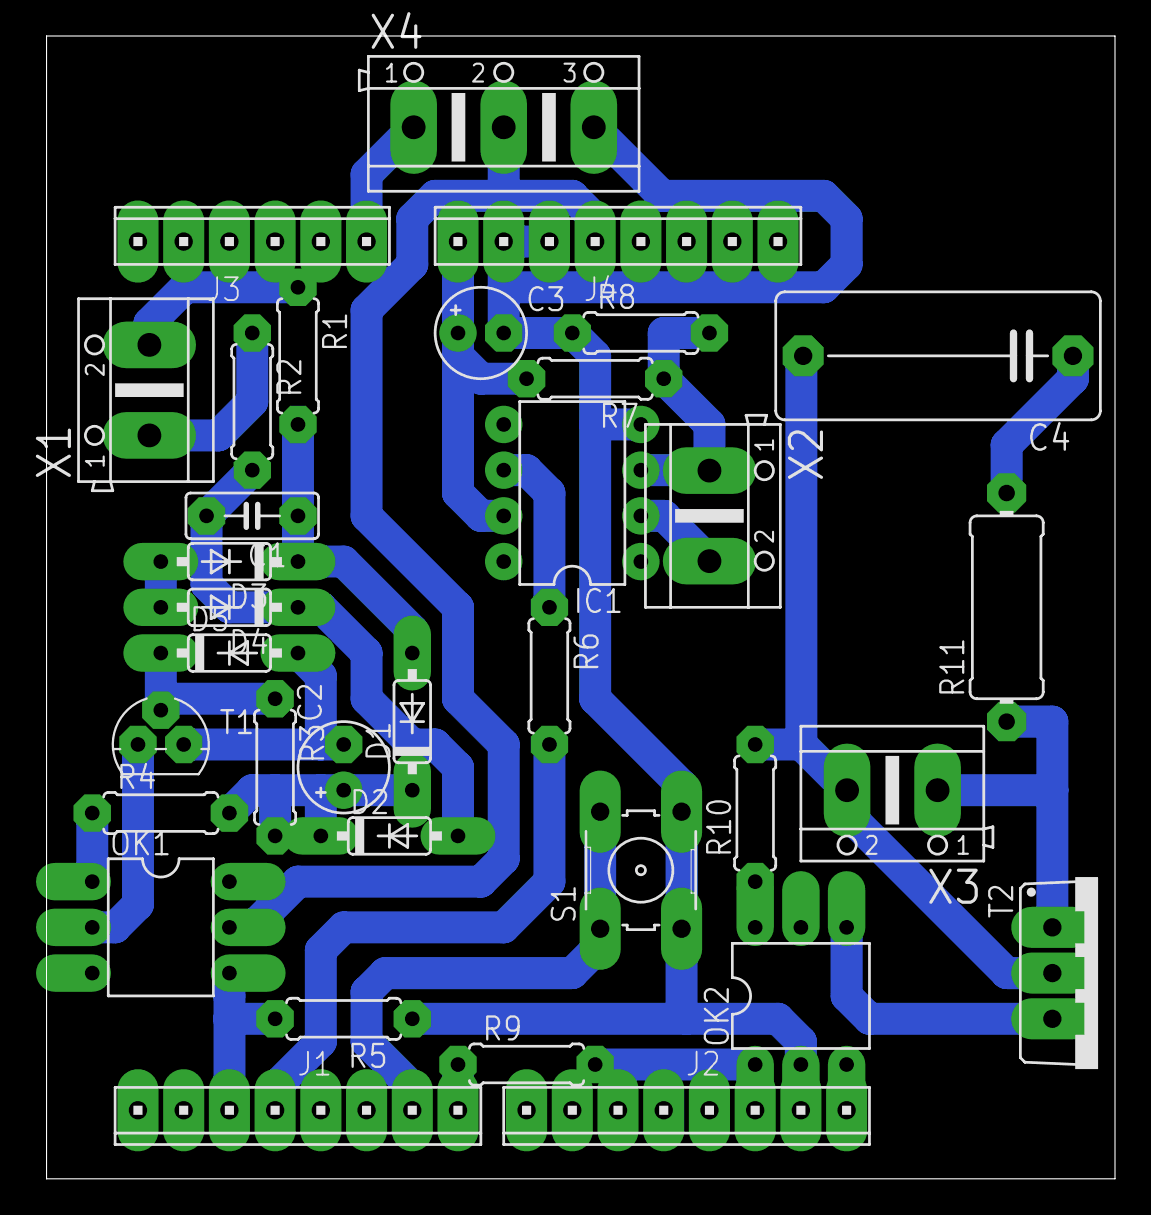
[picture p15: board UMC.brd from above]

Board: 2 copper layers, 59.4 x 63.5 mm, 34 parts (0 on the bottom side), 26 nets.

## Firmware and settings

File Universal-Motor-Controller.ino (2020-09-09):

/**********************************************************************************************
 * Arduino Universal Motor Controller - Version 1.0.2
 * by teo Basili <basili.teo@gmail.com> https://github.com/teo666
 **********************************************************************************************/

//#define TEST_MODE

#include "PID_ASYNC.h"
#include "pin_definition.h"

#define ZCD_FAIL_LIMIT 2500
#define TACHO_FAIL_LIMIT 5000

#include <EEPROM.h>

PID *motor_PID;

volatile uint16_t zcd_tick_log = 0;
volatile uint16_t tacho_tick_log = 0;
volatile uint16_t tick_after_zcd = 0;
volatile uint16_t tick_after_tacho = 0;
volatile uint8_t triac_state = 0;

// questa cosa del delay count mi serve per evitare di usare le funzioni di
// tempo di arduino
volatile uint8_t delay_count = 0;
volatile uint8_t delay_allow = 0;

uint16_t tick_per_phase = 0;

/*in alcune circostanze (dovute a problemi induttivi dal momento che ho potuto
registrarli solamente a motore connesso???) capita che il circuito zcd presenti
dei disturbi che fanno si' che alla sua uscita compaiano dei picchi di tensione
che alterano il corretto fasamento; questi picchi tuttavia hanno una durata
molto breve rispetto al tempo in cui l'onda quadra dello zcd si trova a livello
logico alto, per cui utilizzo questa variabile per distinguere tali valori

- al cambiamento dello stato di uscita dello zdc azzero dei parametri, compreso
zcd_error_correction
- controllo periodicamente (nell-interrupt del timer) il valore di ingresso
dello zcd: se e' HIGH incremento zcd_error_correction altrimenti non faccio
niente
- se dopo un po' di tempo tale valore raggiunge un valore limite (10) allora la
mi sto trovando nel punto un cui lo zcd e' effettivamente in fase e non si e'
presentato il disturbo
*/
volatile uint8_t zcd_error_correction = 0;
volatile uint8_t found_correct_main_phase = 0;

volatile uint8_t tacho_error_correction = 0;
volatile uint8_t found_correct_tacho_phase = 0;

/*
variabili per la lettura dei valori analogici, contengono il valore delle
letture
*/
volatile uint8_t HIGH_ANALOG_REG = 0;
volatile uint8_t LOW_ANALOG_REG = 0;

volatile uint8_t frequency_calc_added = 0;

// il range dell' output va da 0 a 485, a 0 il motore gira a foo 485 val minimo
volatile uint16_t output = 65535; // max value
volatile uint16_t tacho_min_speed_value = 0;
volatile uint16_t tacho_max_speed_value = 0;

uint16_t output_min_speed_value = 0;
uint16_t output_max_speed_value = 0;

// variabili del pid

double Setpoint, Input, Output;
volatile uint8_t computeBarrier = 0;

volatile uint16_t delay_counter = 0;
volatile uint16_t last_delay_counter = 0;

//////////////////// FUNZIONI DI UTILITA' ///////////////////////

uint8_t my_digital_read(uint8_t port_reg, uint8_t bit) {
  if (port_reg & _BV(bit))
    return 1;
  return 0;
}

void limit(volatile uint16_t *val, uint16_t min, uint16_t max) {
  if (*val > max) {
    *val = max;
  } else if (*val < min) {
    *val = min;
  }
}

uint16_t calculate_main_power_frequency() {
  uint8_t frequency_calc = 0;
  uint32_t tick_sum = 0;

  while (frequency_calc < 20) {
    if (frequency_calc_added) {
      frequency_calc_added = 0;
      tick_sum += zcd_tick_log;
      frequency_calc++;
    }
  }

  return tick_sum / 20;
}

void check_programming_button() {
  // se il bottone e' pigiato chiededre di rilasciarlo
  if (!my_digital_read(PIND, PROG_PIN)) {
    Serial.println("Release programming button, please");
    while (!my_digital_read(PIND, PROG_PIN)) {
    }
  }
}

void button_hold_request(void (*loop)(), void (*on_exit)()) {
  while (1) {
    loop();
    if (delay_allow) {
      on_exit();
      break;
    }
  }
}

void loop_read_fun() {
  output =
      map((HIGH_ANALOG_REG << 8) | LOW_ANALOG_REG, 1023, 0, 0, tick_per_phase);
}

//////////////////////////////////////////////////////////////////////

void save_low_speed_exit_fun() {
  tacho_min_speed_value = tacho_tick_log;
  output_min_speed_value = output;
  EEPROM.write(0, tacho_min_speed_value >> 8);
  EEPROM.write(1, tacho_min_speed_value);
  EEPROM.write(2, output_min_speed_value >> 8);
  EEPROM.write(3, output_min_speed_value);
  Serial.print(F("LOW speed tacho set to: "));
  Serial.print(tacho_min_speed_value);
  Serial.print(F(" LOW speed output set to: "));
  Serial.print(output_min_speed_value);
  Serial.println(F(", saving ..."));
}

void save_high_speed_exit_fun() {
  tacho_max_speed_value = tacho_tick_log;
  output_max_speed_value = output;
  if (tacho_max_speed_value > tacho_min_speed_value) {
    Serial.println(F("The HIGH speed must be higher than LOW speed"));
    // se il bottone e' pigiato chiededre di rilasciarlo
    check_programming_button();
    Serial.println(F("try again"));
  } else {
    EEPROM.write(4, tacho_max_speed_value >> 8);
    EEPROM.write(5, tacho_max_speed_value);
    EEPROM.write(6, output_max_speed_value >> 8);
    EEPROM.write(7, output_max_speed_value);
    Serial.print(F("HIGH speed tacho set to: "));
    Serial.print(tacho_max_speed_value);
    Serial.print(F(" HIGH speed output set to: "));
    Serial.print(output_max_speed_value);
    Serial.println(F(", saving ..."));
  }
}

#ifdef TEST_MODE

Coefficient k_param;

String serial_read;

// funzione di ricerca dei parametri del pid

CoefficientPtr search() { return &k_param; }

#else
#include "configuration.h"
#endif

void setup() {

  INIT_TRIAC_LOG();
  INIT_ZCD_LOG();
  INIT_TACHO_LOG();

  INIT_TRIAC();
  INIT_PROG_BUTTON();
  INIT_ZCD();
  INIT_TACHO();

  // abilita le interruzioni sul pin 3 e 2 di arduino (bit meno significativo e'
  // il 2) pin 3 = int1 pin 2 = int0
  EIMSK = 0b00000011;
  ////////////////32

  // interruzioni sul rising e falling edge 01, 11 solo rising
  EICRA = 0b00001111;

  /* configurazione timer 2
   * quindi il valore della variabile putput e' compreso fra 0 e 625
   */

  TCCR2A = 0b00000011;
  TCCR2B = 0b00000001;
  TIMSK2 = 0b00000001;

#ifdef TEST_MODE
  // abilito le interruzioni del timer per la serial.available
  TIMSK0 = 0b00000001;
#else
  // disabilito interruzioni timer 0
  TIMSK0 = 0b00000000;
#endif

  // settaggio della lettura analogica
  // setto il voltaggio di riferimento del convertitore alla tensione di
  // alimentazione e il multiplexer per la lettura
  ADMUX = (1 << 6) | (SPEED_READ & 0x07);

  // abilito l'ADC, le interruzioni hardware e il prescaler a 128 per letture
  // accurate su 10bit
  ADCSRA = 0b10001111;
  // non setto le lettura automatiche utilizzando il registro ADCSRB perche le
  // lancio a mano

  Serial.begin(9600);

  zcd_tick_log = 0;
  tick_after_zcd = 0;

  uint16_t prog_output = 0;

  Serial.println(F("Calculating frequency ..."));
  tick_per_phase = calculate_main_power_frequency();

  Serial.print(F("Number of tick per half period: "));
  Serial.println(tick_per_phase);

  if (!my_digital_read(PIND, PROG_PIN)) {

    Serial.println(F("Programming mode"));

    // se il bottone e' pigiato chiededre di rilasciarlo
    check_programming_button();

    prog_output = (HIGH_ANALOG_REG << 8) | LOW_ANALOG_REG;
    if (prog_output) {
      Serial.println(F("Turn speed potentiometer to lowest value ..."));
      while (prog_output) {
        prog_output = (HIGH_ANALOG_REG << 8) | LOW_ANALOG_REG;
      }
    }

    // se il bottone e' pigiato chiededre di rilasciarlo
    check_programming_button();

    Serial.println(
        F("Turn potentiometer to increase speed and reach desire LOW speed, "
          "once done press and hold programming button ..."));

    button_hold_request(&loop_read_fun, &save_low_speed_exit_fun);

    // se il bottone e' pigiato chiededre di rilasciarlo
    check_programming_button();

    Serial.println(
        F("Turn potentiometer to increase speed and reach desire HIGH speed, "
          "once done press and hold programming button ..."));

    button_hold_request(&loop_read_fun, &save_high_speed_exit_fun);

    Serial.println(F("Configuration completed, enjoy!"));
    // impedisce la modalita' manuale quando si esce dal settaggio
    check_programming_button();
  }
  Serial.println(F("Operating mode"));
  Serial.println(F("Reading paramters ..."));
  tacho_min_speed_value = (EEPROM.read(0) << 8) | EEPROM.read(1);
  output_min_speed_value = (EEPROM.read(2) << 8) | EEPROM.read(3);
  tacho_max_speed_value = (EEPROM.read(4) << 8) | EEPROM.read(5);
  output_max_speed_value = (EEPROM.read(6) << 8) | EEPROM.read(7);
  Serial.print(F("LOW speed tacho value: "));
  Serial.print(tacho_min_speed_value);
  Serial.print(F(", HIGH speed tacho value: "));
  Serial.println(tacho_max_speed_value);
  Serial.print(F("LOW speed output value: "));
  Serial.print(output_min_speed_value);
  Serial.print(F(", HIGH speed output value: "));
  Serial.println(output_max_speed_value);

#ifndef TEST_MODE
  init_params();
#endif

  output = output_min_speed_value;
  Output = output;

  motor_PID = new PID(&Input, &Output, &Setpoint, P_ON_M, &search,
                      &tacho_tick_log, DIRECT);

  // TODO quando sopra un certo livello azzerare il valore di output per rendere
  // il rallentamento migliore
  motor_PID->SetOutputLimits(
      0, output_min_speed_value +
             (abs(tick_per_phase - output_min_speed_value) >> 1));

  motor_PID->SetMode(AUTOMATIC);

#ifndef TEST_MODE
  //Serial.end();
#endif
}

volatile uint8_t _tacho_trig = 0;

void loop() {

  // valore del potenziometro
  Setpoint = map(((HIGH_ANALOG_REG << 8) | LOW_ANALOG_REG), 0, 1023,
                 tacho_min_speed_value, tacho_max_speed_value);

  if (my_digital_read(PIND, PROG_PIN)) {
    motor_PID->SetMode(AUTOMATIC);
    Input = tacho_tick_log;

    if (computeBarrier) {
      motor_PID->Compute();
      computeBarrier = 0;
    }

#ifdef TEST_MODE

    if (delay_counter - last_delay_counter > 60000) {

      if (Serial.available()) {
        serial_read = Serial.readString();
        String K = serial_read.substring(0, 2);

        if (K.equals("kp")) {
          k_param.Kp = serial_read.substring(2).toFloat();
        } else if (K.equals("ki")) {
          k_param.Ki = serial_read.substring(2).toFloat();
        } else if (K.equals("kd")) {
          k_param.Kd = serial_read.substring(2).toFloat();
        } else {
          Serial.print("invalid arguments");
        }

        Serial.print("Kp: ");
        Serial.print(k_param.Kp, 8);
        Serial.print(" Ki: ");
        Serial.print(k_param.Ki, 8);
        Serial.print(" Kd:");
        Serial.println(k_param.Kd, 8);
      }
      Serial.print("Setpoint: ");
      Serial.print(Setpoint);
      Serial.print(" Input: ");
      Serial.print(Input);
      Serial.print(" Output: ");
      Serial.println(Output);
      last_delay_counter = delay_counter;
    }
#endif

    output = Output;

  } else {
    motor_PID->SetMode(MANUAL);
    output = map(((HIGH_ANALOG_REG << 8) | LOW_ANALOG_REG), 0, 1023,
                 tick_per_phase, 0);
  }

  /**
   * rendo il codice invulnerabile ai cambiamenti di frequenza della AC
   * in realta' ad essere precisi dovrei ricalcolare i valori limite di
   * velocita', ma per cambiamenti minimi (che dovrebbero essere la
   * regola) non e' necessario
   * */
  tick_per_phase = zcd_tick_log;

  /**
   * zcd circuit fault: in caso di fault dello zcd disabilito il triac e
   * imposto l'output al massimo valore, equivale a motore spento
   * questa cosa puo' essere fatta anche nel isr, valutare se lasciare qui o
   * spostare
   * */
  if (tick_after_zcd > ZCD_FAIL_LIMIT) {
    output = 65535;
    TURN_OFF_TRIAC();
  }

  /**
   * rilevamento blocco del motore
   * */
  if (tick_after_tacho > TACHO_FAIL_LIMIT) {
    //do something
    //Serial.println("hang detection");
    /*output = 65535;
    TURN_OFF_TRIAC();*/
  }


}

// handler dell' interrupt associato al pin 2 di arduino
// utilizzato per la sincronizzazione di fase, e' connesso
// all'uscita del circuito di ZCD
ISR(INT0_vect) {
  zcd_error_correction = 0;
  found_correct_main_phase = 0;
  // lancia una lettura del valore analogico
  ANALOG_READ();
}

// handler dell' interrupt associato al pin 3 di arduino
// utilizzato per il rilevamento del tacogeneratore
ISR(INT1_vect) {
  tacho_error_correction = 0;
  found_correct_tacho_phase = 0;
}

// interrupt associato al timer, all'interno di una semionda della rete
// effettua dei controlli periodici, quali l'incremento del contatore
// per poter far si che il bottone do programmazione funzioni c'e' bisogno dello
// zcd
ISR(TIMER2_OVF_vect) {
  //
  // zcd
  //
  if (my_digital_read(PIND, ZCD_INPUT)) {
    zcd_error_correction++;
  }

  if (zcd_error_correction > 10 && !found_correct_main_phase) {
    zcd_tick_log = tick_after_zcd;
    frequency_calc_added = 1;
    if (!my_digital_read(PIND, PROG_PIN) && !delay_allow) {
      delay_count++;
    } else {
      delay_count = 1;
      delay_allow = 0;
    }
    if (!delay_count) {
      delay_allow = 1;
    }
    tick_after_zcd = 0;
    // spegni il triac
    TURN_OFF_TRIAC();
    triac_state = 0;
    found_correct_main_phase = 1;
  }
  //
  // tacho
  //
  if (my_digital_read(PIND, TACHO_INPUT)) {
    tacho_error_correction++;
  }

  if (tacho_error_correction > 15 && !found_correct_tacho_phase) {
    tacho_tick_log = tick_after_tacho;
    computeBarrier = 1;
    tick_after_tacho = 0;
    found_correct_tacho_phase = 1;

#ifdef TEST_MODE
    _tacho_trig = !_tacho_trig;
    if (_tacho_trig) {
      TURN_ON_TACHO_LOG();
    } else {
      TURN_OFF_TACHO_LOG();
    }
#endif
  }
  //////////////////////////////////////
  tick_after_zcd++;
  tick_after_tacho++;

  delay_counter++;

  if (tick_after_zcd >= output && !triac_state) {
    // accendi il triac
    TURN_ON_TRIAC();
    triac_state = 1;
  }
}

// al completamento della lettura del valore del potenziometro salva i valori
ISR(ADC_vect) {
  LOW_ANALOG_REG = ADCL;
  HIGH_ANALOG_REG = ADCH;
}

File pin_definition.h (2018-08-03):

#include "utility.h"

#ifndef _PIN_DEFINITION
  #define _PIN_DEFINITION

  //TRIAC OUTPUT
  #define TRIAC_PORT PORTD
  #define TRIAC_STATUS_REG DDRD
  #define TRIAC_OUTPUT 7

  #define INIT_TRIAC()    sbi(TRIAC_STATUS_REG,TRIAC_OUTPUT); cbi(TRIAC_PORT,TRIAC_OUTPUT);
  
  #define TURN_ON_TRIAC() sbi(TRIAC_PORT,TRIAC_OUTPUT)
  #define TURN_OFF_TRIAC() cbi(TRIAC_PORT,TRIAC_OUTPUT)
  
  //PROGRAMMING BUTTON
  #define PROG_BUTTON_PORT PORTD
  #define PROG_BUTTON_STATUS_REG DDRD
  #define PROG_PIN 6

  #define INIT_PROG_BUTTON()  cbi( PROG_BUTTON_STATUS_REG,PROG_PIN); sbi(PROG_BUTTON_PORT,PROG_PIN);

  //ZCD
  #define ZCD_PORT PORTD
  #define ZCD_STATUS_REG DDRD
  #define ZCD_INPUT 2

  #define INIT_ZCD() cbi( ZCD_STATUS_REG , ZCD_INPUT );

  
  //TACHO
  #define TACHO_PORT PORTD
  #define TACHO_STATUS_REG DDRD
  #define TACHO_INPUT 3

  #define INIT_TACHO() cbi( DDRD , TACHO_INPUT ); sbi( PORTD , TACHO_INPUT );
  
  //PORTA READ POT
  #define SPEED_READ 0
  #define ANALOG_READ() sbi( ADCSRA , 6 )




  ///////////////////////// LOG ////////////////////

  //TRIAC LOG
  #define TRIAC_LOG_PORT PORTB
  #define TRIAC_LOG_STATUS_REG DDRB
  #define TRIAC_LOG 5

  #define INIT_TRIAC_LOG() sbi(TRIAC_LOG_STATUS_REG,TRIAC_LOG); cbi(TRIAC_LOG_PORT,TRIAC_LOG);
  
  #define TURN_ON_TRIAC_LOG() sbi( TRIAC_LOG_PORT , TRIAC_LOG )
  #define TURN_OFF_TRIAC_LOG() cbi( TRIAC_LOG_PORT , TRIAC_LOG )
  
  
  //ZERO CROSSING DETECTOR LOG
  #define ZCD_LOG_PORT PORTB
  #define ZCD_LOG_STATUS_REG DDRB
  #define ZCD_LOG 4

  #define INIT_ZCD_LOG() sbi(ZCD_LOG_STATUS_REG,TRIAC_LOG); cbi(ZCD_LOG_PORT,TRIAC_LOG);

  #define TURN_ON_ZDC_LOG() sbi( ZCD_LOG_PORT , ZCD_LOG )
  #define TURN_OFF_ZDC_LOG() cbi( ZCD_LOG_PORT , ZCD_LOG )
  

  //TACHO LOG
  #define TACHO_LOG_PORT PORTB
  #define TACHO_LOG_STATUS_REG DDRB
  #define TACHO_LOG 3

  #define INIT_TACHO_LOG() sbi(TACHO_LOG_STATUS_REG,TRIAC_LOG); cbi(TACHO_LOG_PORT,TRIAC_LOG);
  
  #define TURN_ON_TACHO_LOG() sbi( TACHO_LOG_PORT, TACHO_LOG )
  #define TURN_OFF_TACHO_LOG() cbi( TACHO_LOG_PORT, TACHO_LOG )

#endif

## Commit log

2018-07-21 commit per conclusione parte di alimentazione, inizio parte feedback
2018-07-21 parte relativa all'analisi del segnale di tacho
2018-07-22 fine controllo feedback rozzo, inizio integrazione con PID
2018-07-22 aggiunto controllo PID
2018-07-27 tacho schematic
2018-07-29 dopo il setup disabilitare la modalita manuale
2018-07-30 integrazione PID
2018-07-31 integrazione tabella valori pid
2018-08-03 integrazione button_hold
2018-08-03 rimozione funzione di settaggio all'interno del setup con creazione nuove funzioni separate
2018-08-03 inclusione libreria PID asincrona nel progetto stesso
2018-08-03 rimozione funzioni non utilizzate del pid
2018-08-04 change log
    -aggiunta modalita di test per provare i valori del pid
    -modificata libreria pid per renderla asincrona con il tacho
    -spostamento del codice in file separati
    -il motore risulta ora stabile anche a bassi giri (test parametri pid)
    -le funzioni per la programmazione sono state spostate e rese uniformi con il dice di callback del bottone
2018-08-12 -stabilita' a cambi di frequenza -rilevazione fallimenti zcd -rilevazione motore fermo -riduzione attesa iniziale
    [configuration.h]
2018-08-30 aggiunta progetti eagle
    [UMC.brd, UMC.sch]
2020-09-09 fix macro
    [configuration.h]
